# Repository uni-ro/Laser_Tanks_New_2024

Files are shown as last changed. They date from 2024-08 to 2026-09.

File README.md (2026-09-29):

# Laser Tanks
Laser Tanks is a project run by the Curtin Robotics Club.
Our aim is to make a game of laser tag that is played with remote controlled tanks.
hi from james

## Contents
- [Code](https://github.com/curtinrobotics/Laser_Tanks_New_2024/tree/master/Code)
- [Laser Reciever](https://github.com/curtinrobotics/Laser_Tanks_New_2024/tree/master/Laser%20Receiver)
- [Tank CAD Model](https://github.com/curtinrobotics/Laser_Tanks_New_2024/tree/master/Tank%20CAD%20Model)
- [Tank Motherboard](https://github.com/curtinrobotics/Laser_Tanks_New_2024/tree/master/Tank%20Motherboard)

***

### CAD model
This is the documentation for the tank CAD model.
![[CAD Model#Summary]]

***

### Motherboard
This is the documentation for the tank motherboard.

![[Tank Motherboard]]

***

### Microcontroller Programming  
![[How to write and upload code]]

***

### Remote microcontroller programming  

***

### Laser Detection  

***

### Map Design  

***

### RFID

***

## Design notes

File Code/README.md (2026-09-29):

# Code
This is the guide for how to write code and upload the code to the ESP8266 and ESP32s for Laser Tanks.

## Environment setup
1. **Download VSCode**.
	The programming IDE we are using is Visual Studio Code. You can download it from here: https://code.visualstudio.com/download

2. **Install the required extensions**.
	The required extensions are
	- PlatformIO
	- C/C++
	The recommended extensions are
	- Serial Monitor

3. **Open the the Tank Source folder in VSCode**.
	Once you have VSCode set up, you can open the Tank Source folder. This folder contains everything for programming and uploading. You will know you have opened the correct folder if your explorer looks like this.
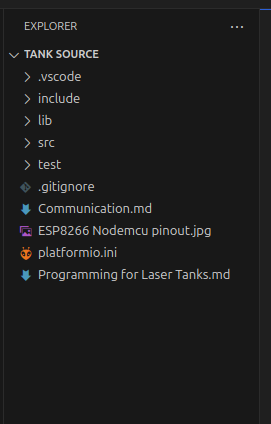
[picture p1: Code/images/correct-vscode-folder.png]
correct vscode folder
	 

## Minimal example
This is an example of how to get a code file compiled and uploaded to the microcontrollers.

### Create the code file
Under the src folder, create a new .cpp file to write the code in.
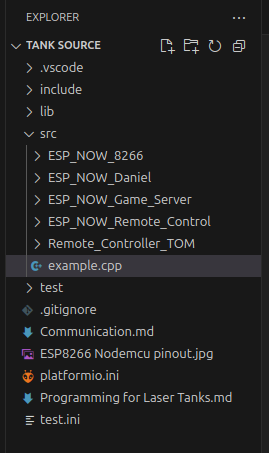
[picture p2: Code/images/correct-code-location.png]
correct code location

The code file needs a few things in it before it can be compiled and uploaded

```cpp title="Minimal example"
#include <Arduino.h>

void setup() {

}

void loop() {

}
```

### Create the platformio.ini configuration.
In order to actually upload to the microcontrollers, you need to create a platformio configuration.
An example platformio configuration looks like this
```ini title="Example platformio"
[env:Configuration_name]
platform = platform_name
board = board_name
framework = framework_name
build_src_filter =
	-<**/*.cpp>
```
- env is the name of your configuration. Put whatever you want there ```[env:Whatever]```
- platform_name refers to the microcontroller you are using. For example ```board = espressif32``` for the ESP32, and ```board = espressif8266``` for the ESP8266.
- board_name refers to what board you are using. If you are unsure, use ```board = nodemcu```
- framework refers to, i dont know just put ```framework = arduino```
- build_src_filter is where you tell platformio which files to compile. Make sure you include the line ```-<**/*.cpp>```. This tells platformio to ignore every code file in the src directory, without this, platformio will try to compile every file at the same time which will lead to errors. Include ```+<path_to_file.cpp>``` for every file you want to include in your configuration. For this example, this will be ```+<example.cpp>```

### Upload to the microcontroller
Now we are ready to upload the code to the microcontroller. First go to the platformio tab on the left.
![[Pasted image 20250313174216.png]]
Then, expand the option with the same name that you put in the ```[env:Whatever]``` and click Upload.
![[Pasted image 20250313174403.png]]

## Troubleshooting
### Board is not detected
If your computer is not detecting the microcontroller

### Uploading through wsl

First install usbipd to windows, if not already installed. To install usbipd, use the command ```winget install usbipd``` in the windows command line
Open a powershell window or command prompt in administrator mode.
Use the command ```usbipd list``` to find a list of all connected usb devices.
Find the device required and take note of the bus id under the "BUSID" column.
If this is the first time connecting the device, run the command ```usbipd bind -b {BUSID}``` where {BUSID} is the id of the usb to attach
Next, attach this to the wsl system by using the following command ```usbipd attach --wsl --busid {BUSID}``` where {BUSID} is still the id of the usb to attach.
This should attach the usb to the wsl system.
In wsl, run ```dmesg``` to find which port the device was attached to.
If the port is not found, run the following command ```sudo modprobe cp210x```. The port should now be found.
VSCode may state that there is an access denied error which can be fixed by running ```sudo chmod 777 {PORT}``` where {PORT} is the full path to the attached usb port.

This is also explained in the following guide: https://developer.espressif.com/blog/espressif-devkits-with-wsl2/

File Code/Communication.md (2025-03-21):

This is the communication between the tank and controller.
The tank communicates using both Serial and ESPNow.

The communication is very simple in an effort to make it more expandable.
The first byte, ignoring start byte for serial, is the message header and signifies what kind of message you are sending.
The rest of the message can be used however in accordance to the kind of message header.
The only restriction is bytes ```0xFF``` and ```0xFE```. These are reserved for the serial start and end bytes. Even when using ESPNow these bytes may not be used.
The maximum length of a message is 255 bytes, we should not even be getting close to this.

There is a difference between Serial and ESPNow. The difference is that ESPNow is sent and recieved as the entire message, no start of message or end of message bytes are needed. Serial however, is sent only 1 byte at a time. This means that a start byte and end byte is required.

## Serial communication differences
Serial communication requires an extra byte marking the start of the message, and an extra one for the end of message.
The start of the message is signified by a ```0xFF``` or ```255```
The end of the message is signified by a ```0xFE``` or ```254```

## ESPNow communication differences
ESPNow handles the protocol for you, as such a start byte and end byte is not included.

## Messages
Here is a list of all the message types and how to use them

| First byte | Message type |
| --- | --- |
| 0x00 | Ping |
| 0x01 | Left motor speed  |
| 0x02 | Right motor speed |

### Ping - 0x00
The ping message is used to check if the controller is communicating with the tank, or if the tank is communicating with the controller. 

|Byte number|Options|Description|
|---|---|---|
|0|0x00|Signifies the message type is a ping|
|1|0x00 or 0x01|Signifies whether the message is a ping - 0x00, or a response to a ping 0x01|

### Left motor speed - 0x01
This message is used to tell the tank to set the left motor to a specific speed

| Byte number | Options | Description |
| --- | --- | --- |
| 0 | 0x01 | Signifies the message type is setting the left motor speed |
| 1 | 0x00 - 0x3F, 0x40 - 0x7F | Speed and direction of the motor. Forward between 0x00 - 0x3F where 0x00 is slowest and 0x3F is fastest. Backward between 0x40 - 0x7F where 0x40 is slowest and 0x7F is fastest |

### Right motor speed - 0x02
This message is used to tell the tank to set the right motor to a specific speed

| Byte number | Options | Description |
| --- | --- | --- |
| 0 | 0x02 | Signifies the message type is setting the right motor speed |
| 1 | 0x00 - 0x3F, 0x40 - 0x7F | Speed and direction of the motor. Forward between 0x00 - 0x3F where 0x00 is slowest and 0x3F is fastest. Backward between 0x40 - 0x7F where 0x40 is slowest and 0x7F is fastest |

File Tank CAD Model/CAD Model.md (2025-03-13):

## Summary
This is where all the different versions of the tank 3D model are stored.
Each different version was 3D printed, tested and then improved upon.
This is the current version
![[Tank model V4#Overview]]

## Versions

- [[Tank model V2]]
- [[Tank model V3]]
- [[Tank model V4]]

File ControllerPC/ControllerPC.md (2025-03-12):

This is the code that will run on your computer and control the laser tank.

TODO: Write more here

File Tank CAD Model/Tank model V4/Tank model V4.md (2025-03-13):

## Overview
This is the 4th version of the Laser Tank model. It aims to address issues in the V3 model such as
- The screw holes being slightly too small
- The axle holes being slightly too small
- The driver wheel being too close to the idler wheel
- The accidental shallow screw inset holes in the front track holder
- The holder for the switch and two LEDs being too thin
- The corner of the front track holders needing to be clipped to fit properly

A big change made in V4 is the back tracks not being adjustable anymore. Instead, the tracks were modelled and measured. The required length of tracks was found to be roughy 356 mm
![[Pasted image 20250123214053.png|1400]]

![[IMG_2936.jpg|1400]]
![[IMG_2934.jpg|700]] ![[IMG_2935.jpg|700]]

## Parts
These are the parts needed to build the Tank model V4. It reflects roughly the total cost of building this from scratch.

|Part|Supplier|Cost|
|---|---|---|
|ESP826 Dev board|https://www.makerstore.com.au/product/elec-nodemcu-esp8266/|$14|
|Twin motor gearbox|https://www.pololu.com/product/61|$21|
|Track and wheel set|https://core-electronics.com.au/tamiya-70100-track-and-wheel-set.html|$23|
|2S Li-Po battery|https://hobbytechtoys.com.au/products/hpi-plazma-7-4v-600mah-10c-lipo-battery-pack-160838|$20|
|Total| |$78|

This table does not include everything. For example the breadboard, and wires and stuff.

## Advantages
- Having the back tracks be at a fixed position improves the visuals of the back of the tank. We no longer have an awkward overhanging area
![[back of tank.jpg|700]]

- Having the back tracks be at a fixed position removes the long thin section of PLA that is prone to bending
![[bendy back.jpg|700]] ![[non bendy back.jpg|700]]

- The section that holds the switch and LEDs holds them really firmly and nicely. Giving enough room to connect wires to it
![[switch holder.jpg|700]]

- The section that holds the protoboard holds it really nicely and firmly while being not too difficult to slide in
![[proto board 1.jpg|700]] ![[proto board 2.jpg|700]]

## Issues

- One of the clips that hold the protoboard is broken 
- ![[broken clip.jpg|800]]

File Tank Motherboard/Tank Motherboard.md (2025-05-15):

Here is the documentation for the tank motherboard.

Versions
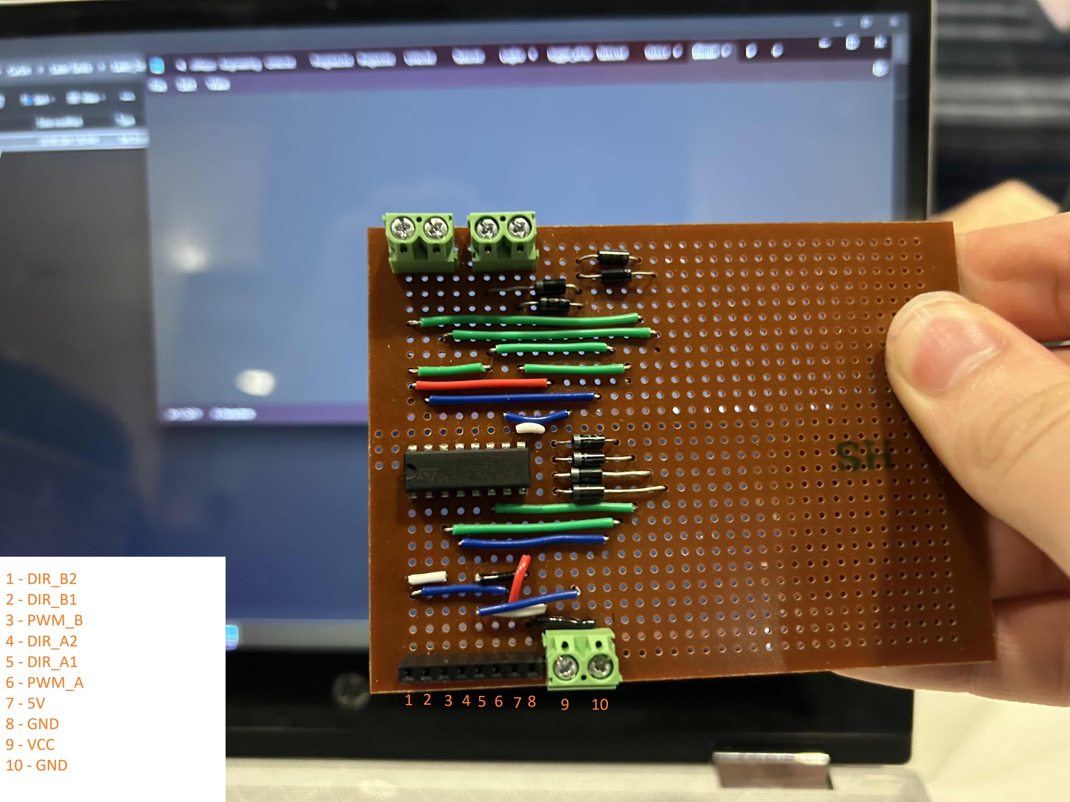
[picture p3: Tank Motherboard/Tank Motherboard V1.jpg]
- 
- [[Tank Motherboard V2.excalidraw]]
- [[Tank Motherboard V3]]

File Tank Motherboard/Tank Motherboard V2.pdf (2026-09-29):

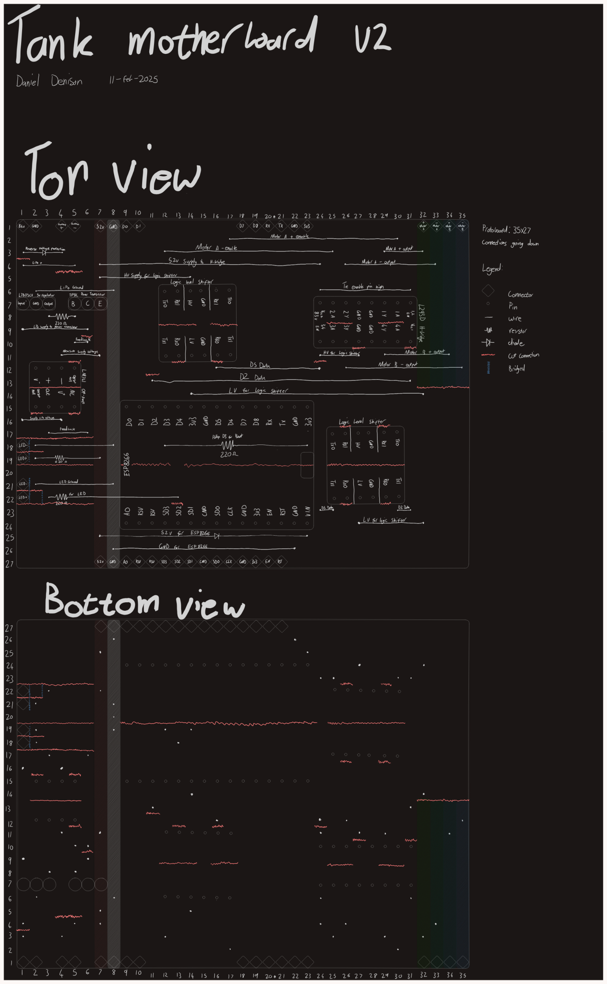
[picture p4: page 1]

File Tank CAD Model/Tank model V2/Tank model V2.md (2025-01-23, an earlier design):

## Overview
This is the 2nd version of the Laser Tanks model.

![[IMG_2780.jpg|1000]]
![[IMG_2781.jpg|500]] ![[IMG_2782.jpg|500]]

## Parts
These are the parts needed to build the Tank model V2. It reflects roughly the total cost of building this from scratch.

|Part|Supplier|Cost|
|---|---|---|
|ESP826 Dev board|https://www.makerstore.com.au/product/elec-nodemcu-esp8266/|$14|
|Twin motor gearbox|https://www.pololu.com/product/61|$21|
|Track and wheel set|https://core-electronics.com.au/tamiya-70100-track-and-wheel-set.html|$23|
|2S Li-Po battery|https://hobbytechtoys.com.au/products/hpi-plazma-7-4v-600mah-10c-lipo-battery-pack-160838|$20|
|Total| |$78|

This table does not include everything. For example the breadboard, and wires and stuff.

## Advantages
- Using nuts where they are being pulled further into their sockets works very well
![[Nuts being pulled in are good.jpg|500]]

## Issues

- Because the tank tracks are under tension, they are pulling the front track holders and the back track holders together, causing the top plate to bend
![[Top plate bending.jpg|500]]

- The breadboard holder is a little bit too short
![[Badly sized breadboard holder.jpg|500]]

- The motor driver circuit is places as far as possible from the motors. For some reason...

- The tank tracks have a large footprint on the ground which adds a bunch of friction while turning

- The channels the screws holding the back track holders screw into are too thin. They are being bent outwards by the screws
![[Not enough screw clearance.jpg|500]]

- The tank is a little bit too wide. The wheels are popping off

- Nuts appear to be unsuitable for screwing screws into, where the nuts are being pulled out.
![[Nuts being pulled out are bad.jpg|500]]
Superglue was even used here to secure the nuts in place but it doesnt seem to be enough.

- No propper place to put a battery, battery is secured with cable ties

- No propper place to put the motor driver, the circuit is secured in with cable ties

- There is nowhere for a switch to go

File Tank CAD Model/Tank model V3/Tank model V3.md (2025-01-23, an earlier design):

## Overview
This is the 3rd version of the Laser Tank model.
This version addresses some of the problems realised with V2, namely
- The motor driver circuit being far from the motors
- The channels for the screws for the back tracks being too small
- Nowhere for a switch to go

Version 3 also includes a space for 2 LEDs for showing anything

![[V3 pic 1.jpg|1200]]
![[V3 pic 2.jpg|600]] ![[V3 pic 3.jpg|600]]

## Parts
These are the parts needed to build the Tank model V3. It reflects roughly the total cost of building this from scratch.

|Part|Supplier|Cost|
|---|---|---|
|ESP826 Dev board|https://www.makerstore.com.au/product/elec-nodemcu-esp8266/|$14|
|Twin motor gearbox|https://www.pololu.com/product/61|$21|
|Track and wheel set|https://core-electronics.com.au/tamiya-70100-track-and-wheel-set.html|$23|
|2S Li-Po battery|https://hobbytechtoys.com.au/products/hpi-plazma-7-4v-600mah-10c-lipo-battery-pack-160838|$20|
|Total| |$78|

This table does not include everything. For example the breadboard, and wires and stuff.

## Advantages
- The threaded inserts work very well. If you make the part fit the smaller diameter at the front of the insert and fit the entire length. They are very easy to insert with a soldering iron and will grip on much tighter than a hex nut
![[Threaded insert.jpg|500]]
- The screw inset depth is perfect to make these rounded M3 screws flush with the top of the body
![[Flush screws.jpg|500]]

## Issues
- Holes for the axles to go through are still too small, needing to hammer the axles in
![[Small axles.jpg|500]]
- Holes for the threaded inserts in the front tracks were accidentally too shallow. 
- The driver wheel is too close to the idler wheel next to it. When using tight tracks, they rub against each other causing a lot of friction
![[Driver and idler wheel too close.jpg|500]]
- The section for fitting the switch and LEDs is too thin. It broke apart while I was trying to remove the support structure
![[Switch and LED holder too thin.jpg|500]]
- The front track holders get too close to the screw holes for the gearbox. The corners need to be cut so that it can fit
![[Cut corners.jpg|500]]
- The holes for the screws are a tiny bit too small, the screws don't fall easily through the holes. Not really an issue because the screws can be easily screwed through, but would be nicer if that was not needed

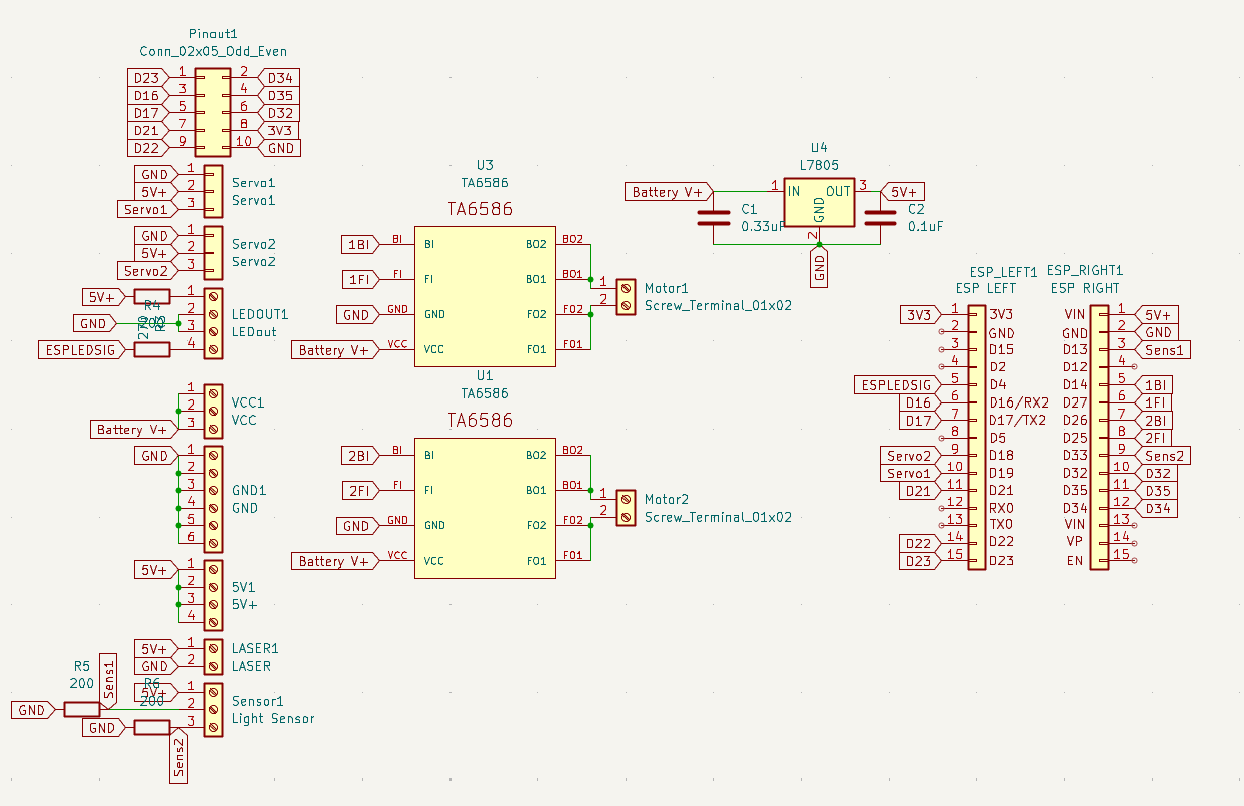
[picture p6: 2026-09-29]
Tank Motherboard/LasertanksPCB_KiCad/motorcontroller/LaserTankPCBV1_Schematic.png

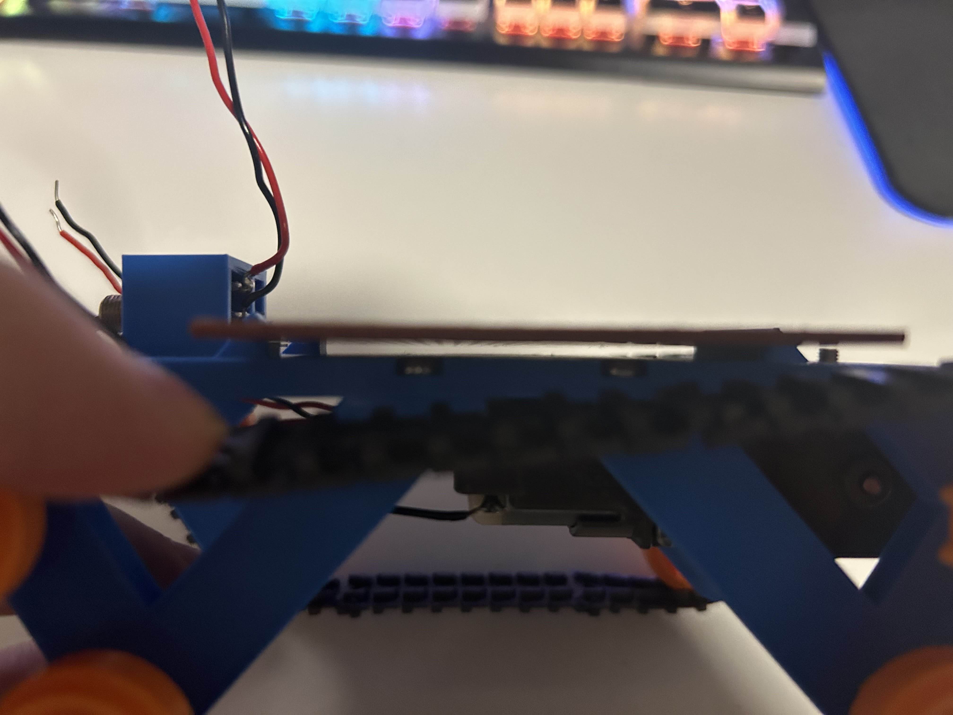
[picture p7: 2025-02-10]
Tank CAD Model/Tank model V4/proto board 2.jpg

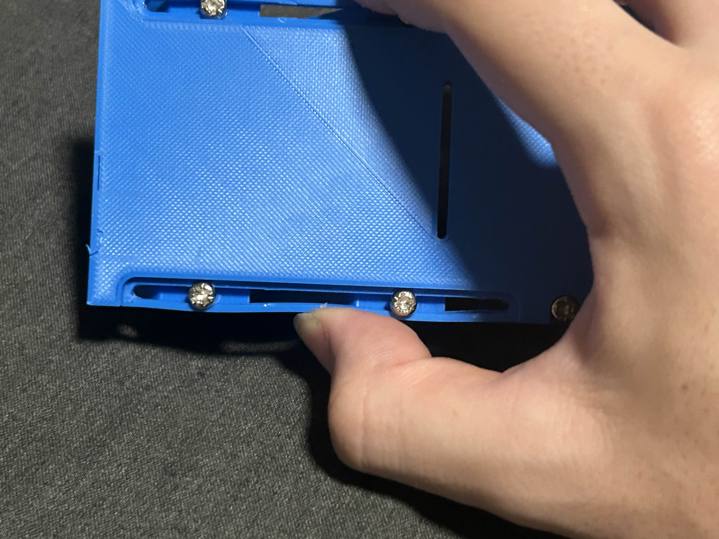
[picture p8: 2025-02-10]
Tank CAD Model/Tank model V4/bendy back.jpg

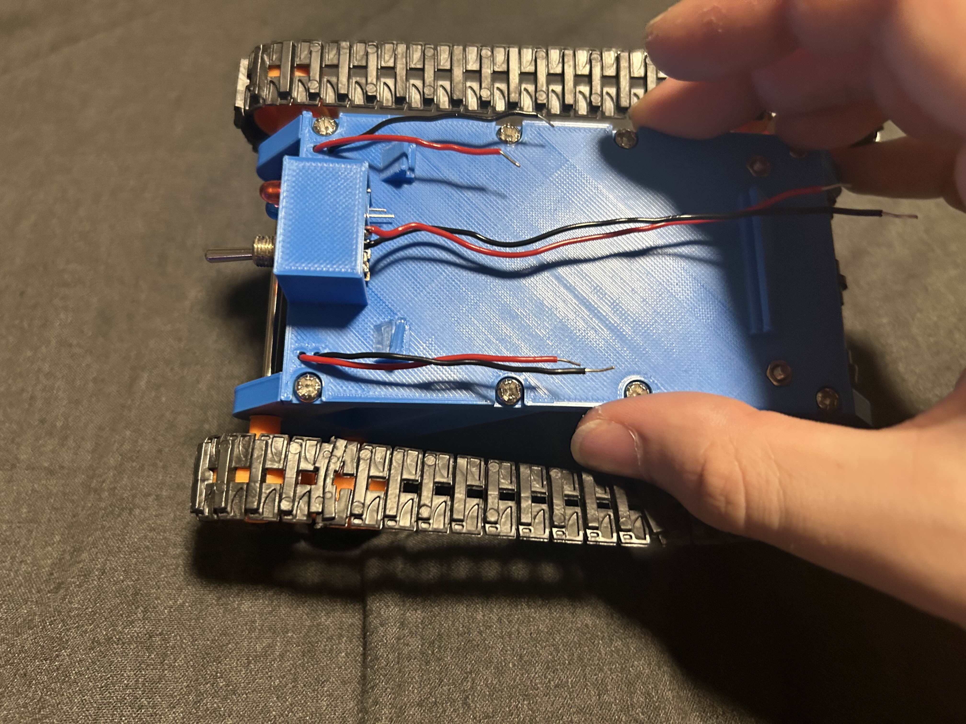
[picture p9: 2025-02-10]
Tank CAD Model/Tank model V4/non bendy back.jpg

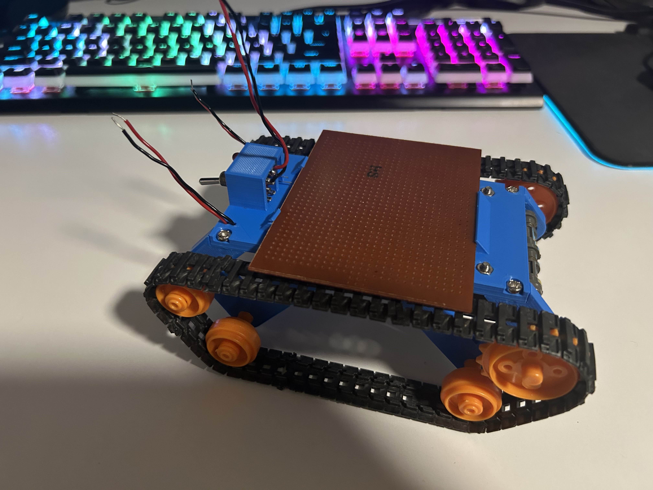
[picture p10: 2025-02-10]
Tank CAD Model/Tank model V4/proto board 1.jpg

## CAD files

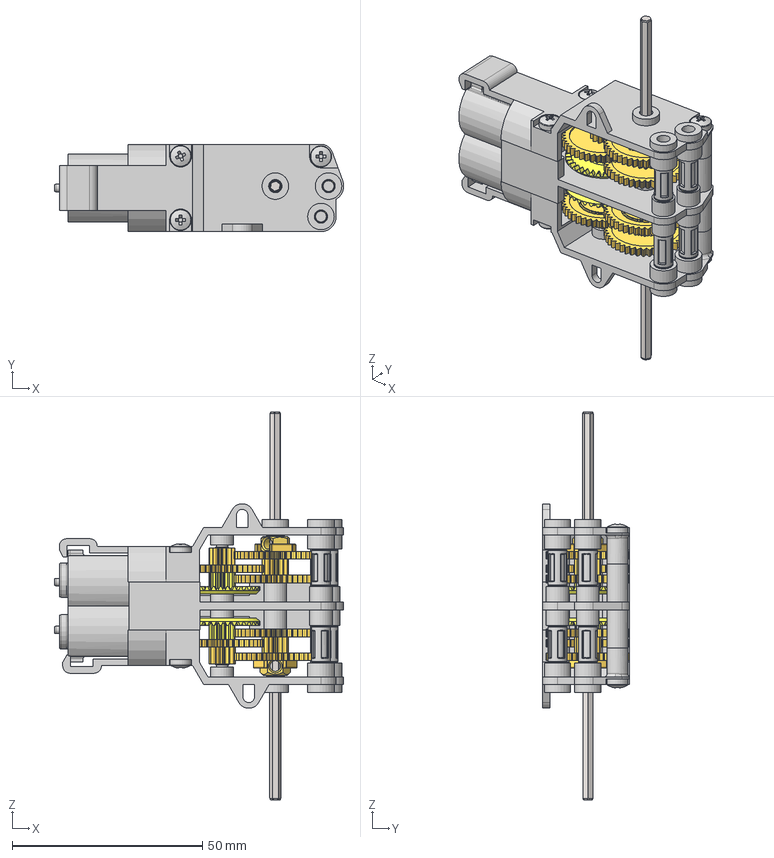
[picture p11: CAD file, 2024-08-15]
Tank CAD Model/STEP files/Motor.step
76.1 x 23.0 x 102.0 mm
middle
motor_1 x 2
left
right
DG_brass_gap4.0 x 12
DG_gold_brass x 2
DG_purple_8_mtr x 2
DG_shaft_23mm x 2
DG_shaft_50mm x 2
DG_yellow_34_12_N01 x 2
TG_G3 x 2
TG_G2 x 4
middle pin x 4
Pan Head Cross Recess Screw_DIN x 6

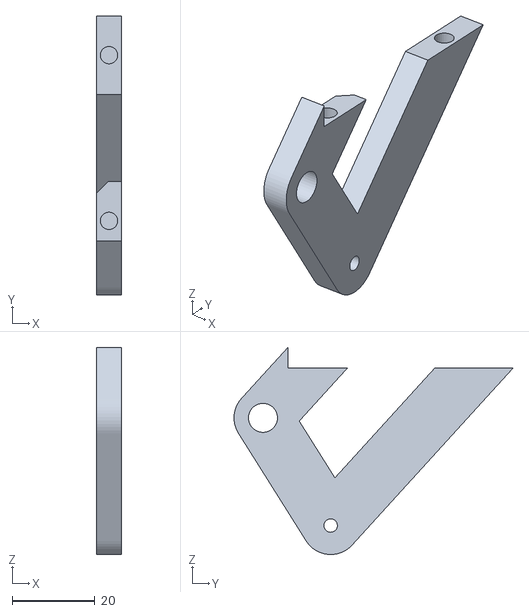
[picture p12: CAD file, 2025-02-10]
Tank CAD Model/Tank model V4/Front track holder L.stl
6.00 x 67.4 x 50.0

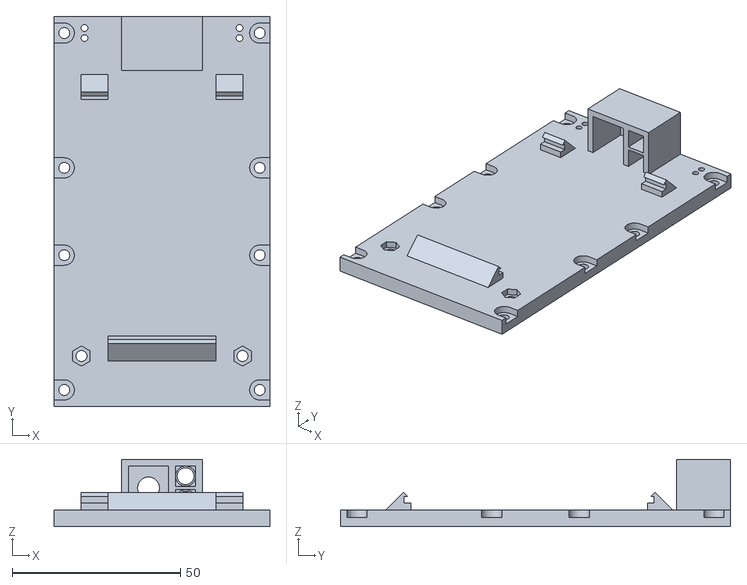
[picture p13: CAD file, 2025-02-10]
Tank CAD Model/Tank model V4/Top plate.stl
64.0 x 115.8 x 20.0

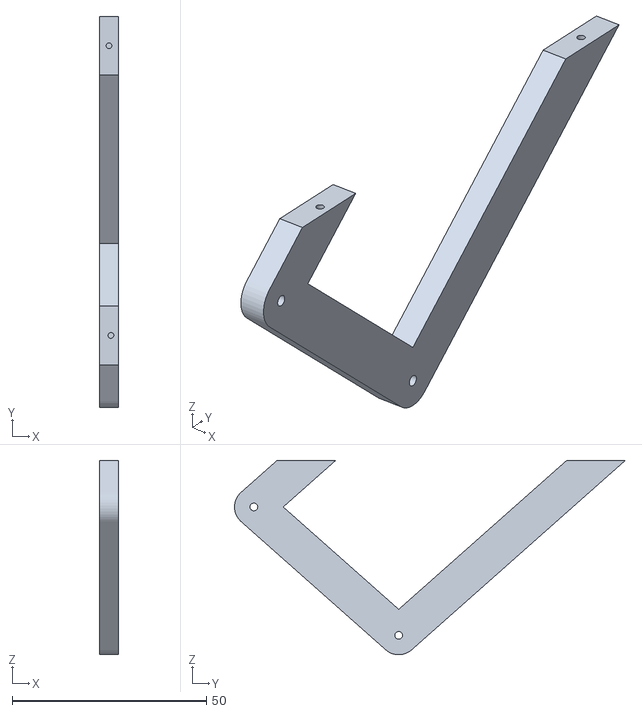
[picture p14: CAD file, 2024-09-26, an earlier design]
Tank CAD Model/Tank model V1/Front track.stl
5.00 x 100.5 x 50.0

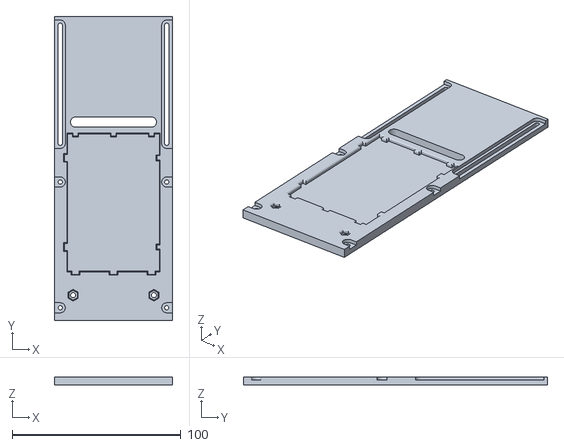
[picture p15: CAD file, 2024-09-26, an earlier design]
Tank CAD Model/Tank model V2/Top plate.stl
70.0 x 180.0 x 5.00

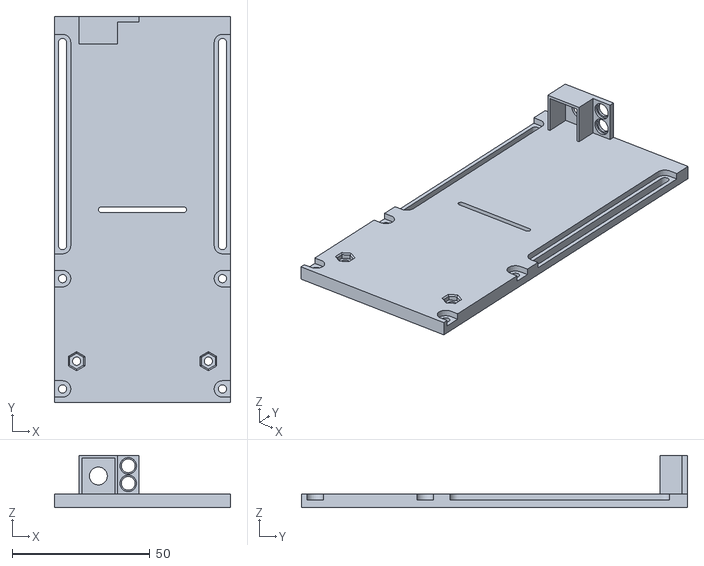
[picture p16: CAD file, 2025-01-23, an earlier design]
Tank CAD Model/Tank model V3/Top plate.stl
64.0 x 140.0 x 19.0

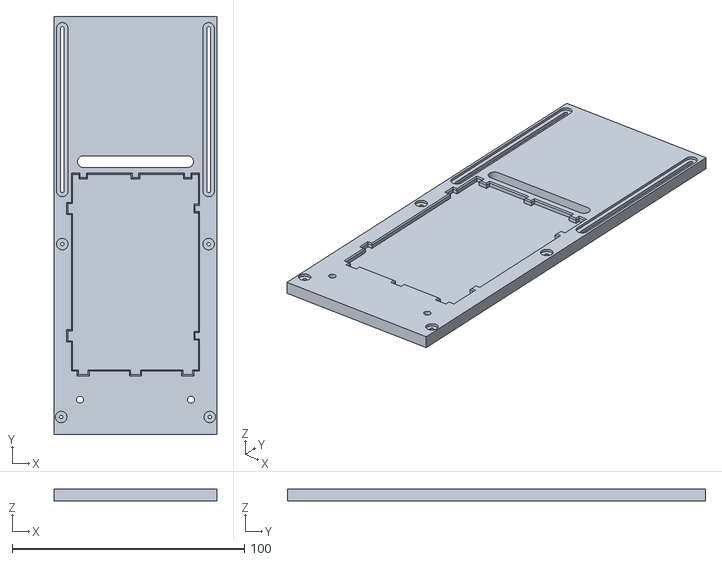
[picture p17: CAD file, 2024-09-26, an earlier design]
Tank CAD Model/Tank model V1/Top plate.stl
70.0 x 180.0 x 5.00

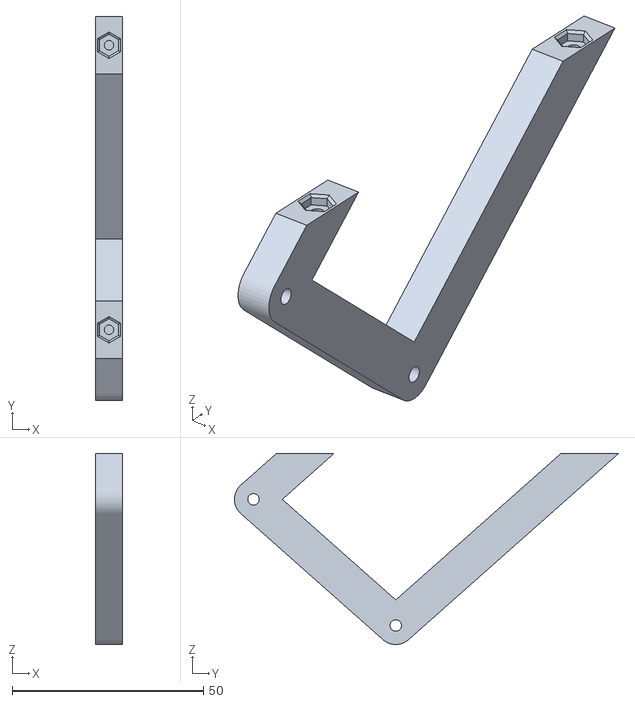
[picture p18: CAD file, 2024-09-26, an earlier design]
Tank CAD Model/Tank model V2/Front track holder.stl
7.00 x 100.5 x 50.0

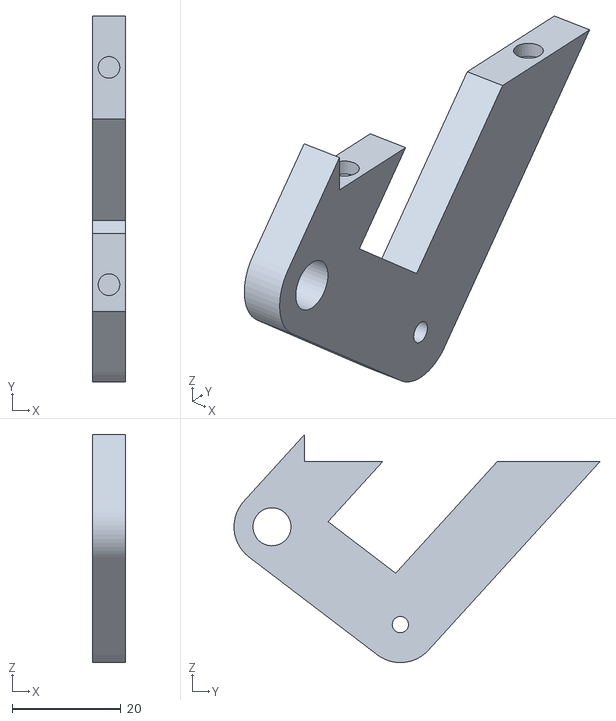
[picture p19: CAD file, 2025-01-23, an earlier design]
Tank CAD Model/Tank model V3/Front track holder.stl
6.00 x 67.4 x 42.0

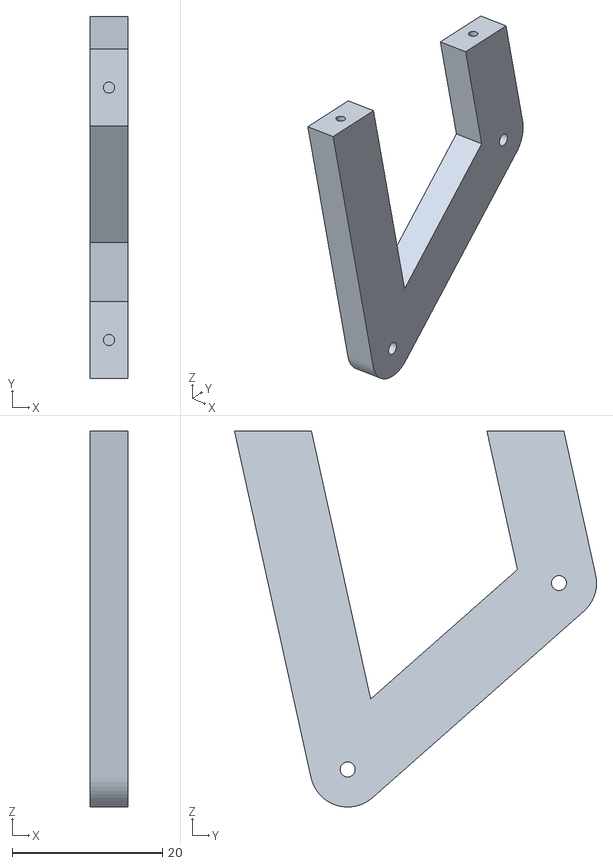
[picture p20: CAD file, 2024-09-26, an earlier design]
Tank CAD Model/Tank model V1/Back track.stl
5.00 x 48.1 x 50.0

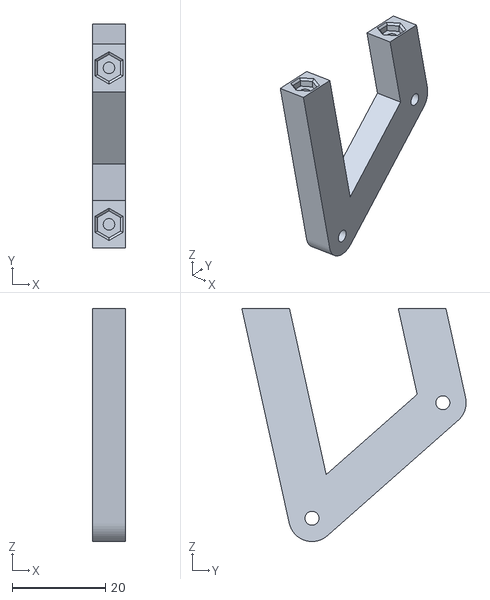
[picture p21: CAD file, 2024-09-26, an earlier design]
Tank CAD Model/Tank model V2/Back track holder.stl
7.00 x 48.1 x 50.0

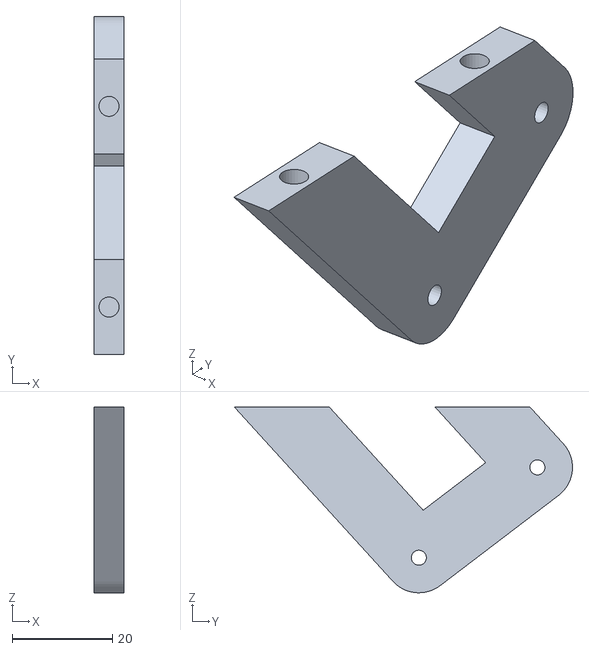
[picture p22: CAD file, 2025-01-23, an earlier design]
Tank CAD Model/Tank model V3/Back track holder.stl
6.00 x 67.4 x 37.0

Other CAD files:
Tank CAD Model/Tank model V4/Back track holder.stl
Tank CAD Model/Tank model V4/Front track holder R.stl
Tank CAD Model/Tank model V1/Top plate skew.stl

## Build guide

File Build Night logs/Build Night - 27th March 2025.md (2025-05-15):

- Tom is helping Blake learn to program on an arduino nano. Trying to blink a laser diode
- Got Thomas started on the turret for the tank. Invited him to the Fusion360 group.
- Emma and Gabriel are mucking around with the raspberry pi.

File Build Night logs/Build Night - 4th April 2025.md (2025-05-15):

- Blake and Tom working on ramping up motor
- Emma is workign on stopping the tank if the controller disconnects

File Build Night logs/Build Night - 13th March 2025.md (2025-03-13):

## Attendees
- Daniel
- Tom
- Gabriel
- Blake
- Silas
- Emma

## Progress
- We have been struggling with an issue with the motors on the tank. We are using little DC motors with gears attached to drive the tracks. However, the gear that attaches to one of the motors was not propperly joined to the motor, causing the motor shaft to spin without turning the tracks. We found 2 motors in the club room that have the gears propperly attaches. We swapped out the bad motor for the good one and the tank is now driving like perfect again.
- I (Daniel) have been designing a PCB to replace the protoboard on the current tank. A PCB is going to be way smaller and cleaner than anything I could do on the protoboard. The design is not finished yet, but I will order it ASAP.
- Once the PCB arrives Ill (Daniel) start working on the next version of the tank model. I will design it to propperly hold the PCB in place, probably with screws. 
- Gabriel came up with a concept for a turret
- We are getting really close to the point where we could attach and use a turret. Once wee have the PCB,

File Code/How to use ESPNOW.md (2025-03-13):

ESPNOW is the communication protocol we are using for the controller / tank communication.
ESPNOWs implementation differs depending on whether you are programming an ESP32 or ESP8266.

## ESPNOW for ESP32
This is how you implement ESPNOW for the ESP32.
### Header files
To use ESPNOW on the ESP32 you need to include the following header files
```cpp title="Required header files for ESPNOW on the ESP32"
#include <WiFi.h>
#include <esp_wifi.h>
#include <esp_now.h>
```

### Initialisation
To set up ESPNOW, use the following code in your setup function
```cpp title="ESPNOW setup code"
// Make sure the ESP32 is in the correct WiFi mode
WiFi.disconnect();
WiFi.mode(WIFI_STA);

uint8 peer_address[] = {0x00, 0x00, 0x00, 0x00, 0x00, 0x00}

esp_now_peer_info_t info;
info.channel = 0;
info.encrypt = false;
memcpy(info.peer_addr, slave_address, 6);

esp_now_init();
esp_now_add_peer(&info);
```

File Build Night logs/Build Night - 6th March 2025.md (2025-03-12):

## People
- Daniel
- Tom
- Gabriel
- Blake
- Silas
- Emma

## Progress
- Team building
- Gabriel working on battery holder
- Blake learning fusion, happy to work on the turret design
- Silas is working on laser reciever stuff
- Tom is working on the controller code
- Emma is working on controller code
- Steve is doing RFID

## Needed materials

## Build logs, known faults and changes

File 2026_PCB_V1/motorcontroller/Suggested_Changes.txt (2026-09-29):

Needs pin header for battery not terminal blocks
the traces between the battery to motor drivers to motor terminals seem a bit thin
should have a pin out headers for a motor rather than a servo and possibly another motor driver on the pcb as the turret has 1 dc motor plus servo not 2 servos
there are slight clearance issues at the top of the pcb due to the over hang from the esp32, though this is very minor 
might be helpful to have more pin headers rather than terminal blocks for breaking out the battery + and 5v  
Needs silkscreen labs for + and - on things like the led terminal blocks

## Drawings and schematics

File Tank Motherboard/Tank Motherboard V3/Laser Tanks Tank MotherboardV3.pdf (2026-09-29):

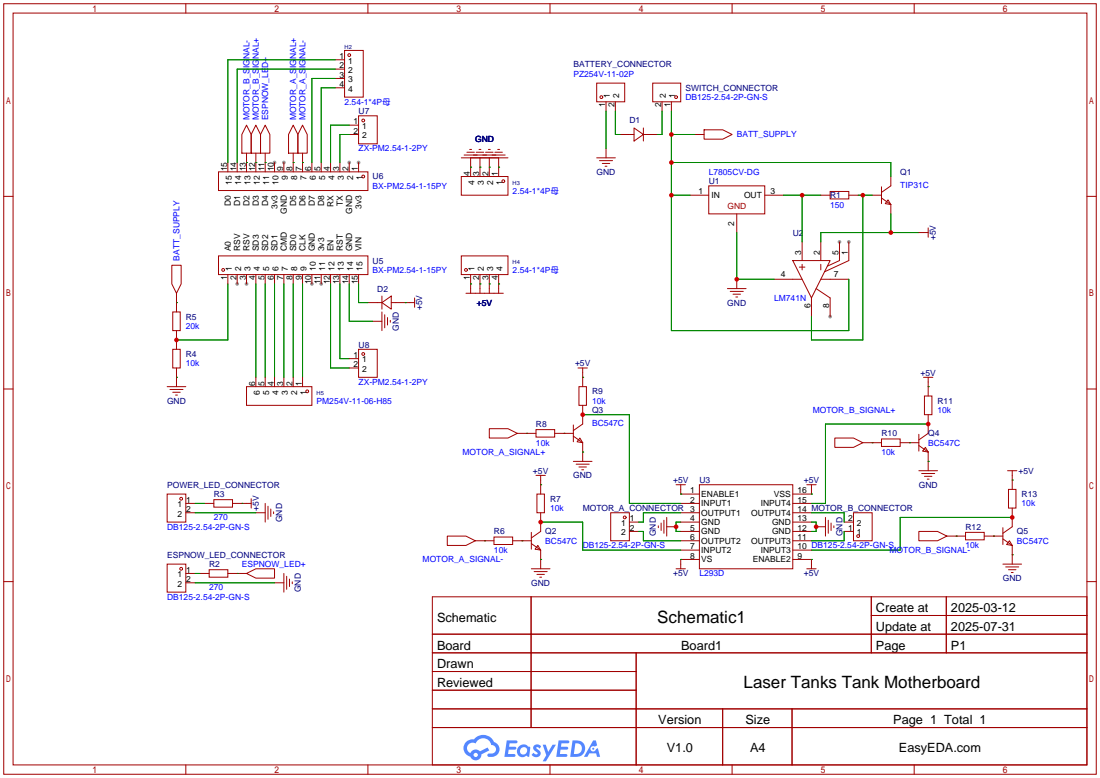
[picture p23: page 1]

Schematic | Schematic1 | Create at | 2025-03-12

Update at | 2025-07-31

Board | Board1 | Page | P1
Drawn | | Laser Tanks Tank Motherboard
Reviewed

Version | Size | Page 1 Total 1
V1.0 | A4 | EasyEDA.com

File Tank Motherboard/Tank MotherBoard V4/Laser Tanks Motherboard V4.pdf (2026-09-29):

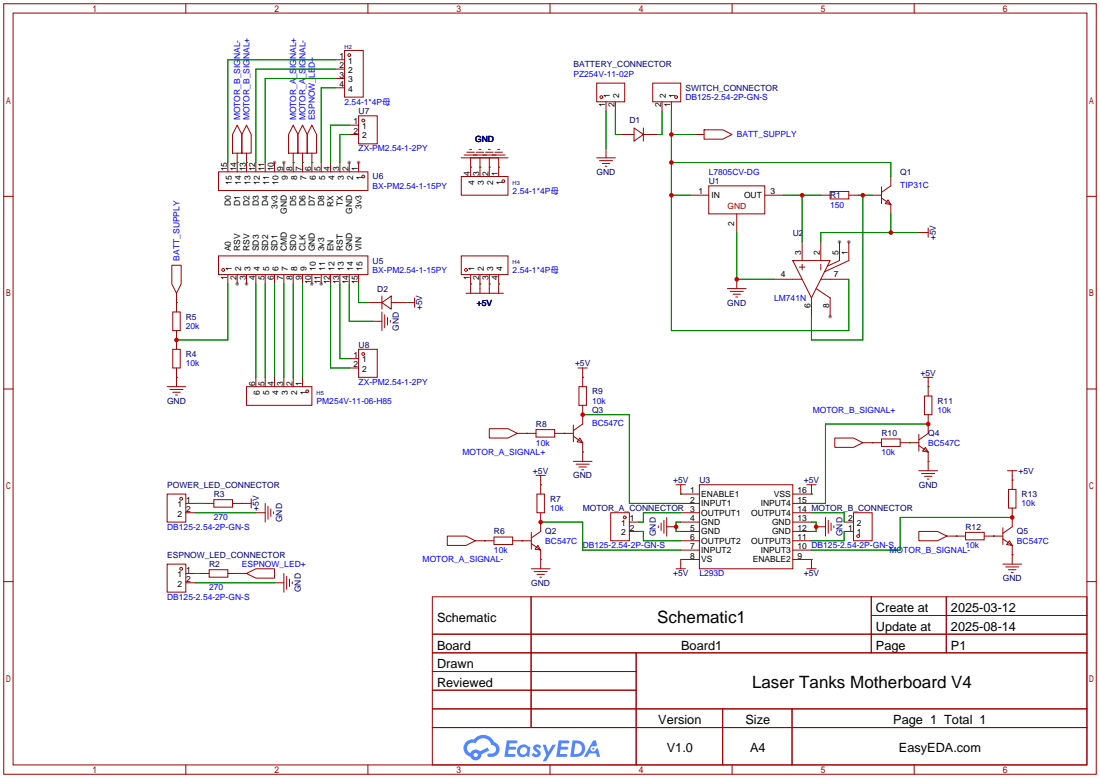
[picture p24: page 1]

Schematic | Schematic1 | Create at | 2025-03-12

Update at | 2025-08-14

Board | Board1 | Page | P1
Drawn | | Laser Tanks Motherboard V4
Reviewed

Version | Size | Page 1 Total 1
V1.0 | A4 | EasyEDA.com

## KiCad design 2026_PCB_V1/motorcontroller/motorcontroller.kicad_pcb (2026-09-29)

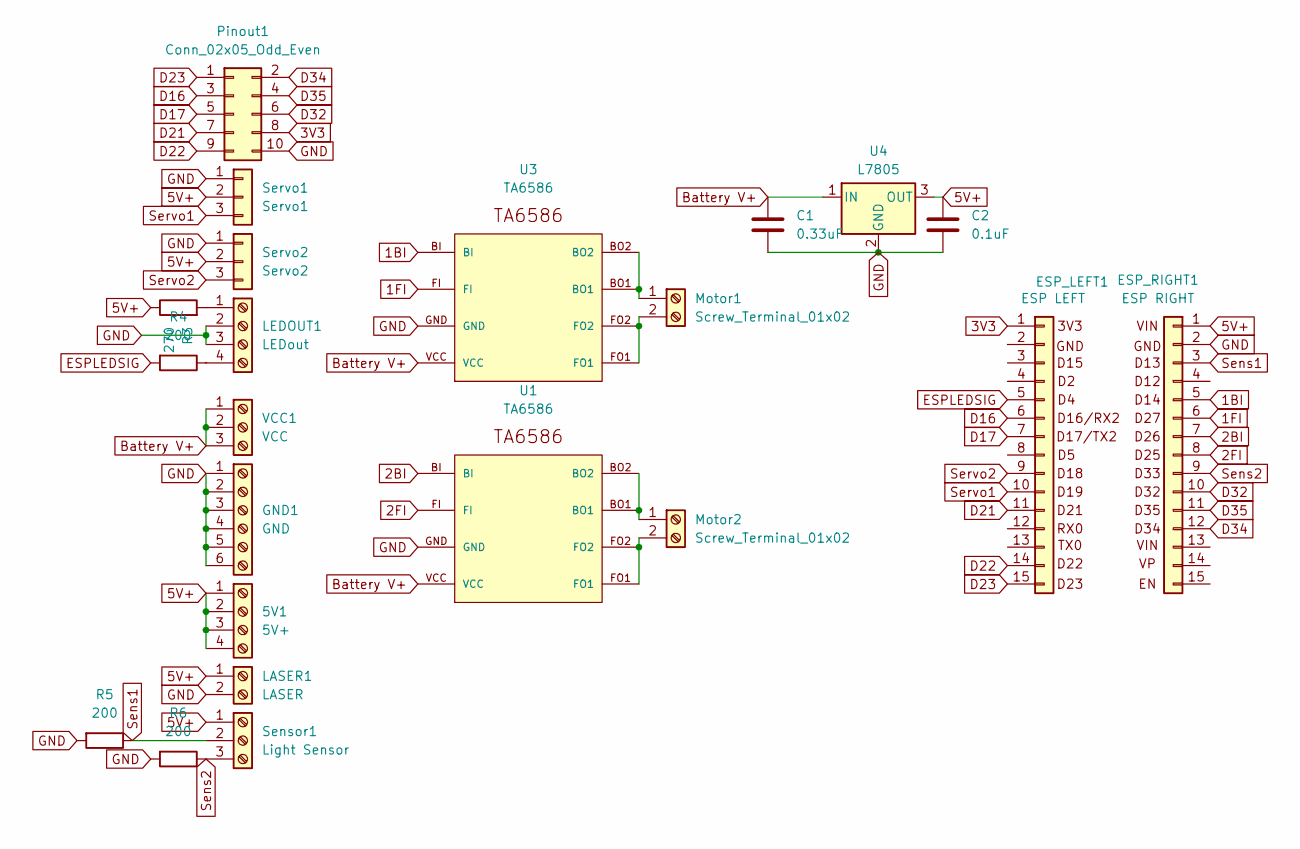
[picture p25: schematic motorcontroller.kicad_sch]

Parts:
5V1: 5V+; TerminalBlock_4Ucon_1x04_P3.50mm_Horizontal
C1: 0.33uF; C_Rect_L9.0mm_W2.5mm_P7.50mm_MKT
C2: 0.1uF; C_Rect_L9.0mm_W2.5mm_P7.50mm_MKT
ESP_LEFT1: ESP LEFT; PinHeader_1x15_P2.54mm_Vertical
ESP_RIGHT1: ESP RIGHT; PinHeader_1x15_P2.54mm_Vertical
GND1: GND; TerminalBlock_4Ucon_1x06_P3.50mm_Horizontal
LASER1: LASER; TerminalBlock_4Ucon_1x02_P3.50mm_Horizontal
LEDOUT1: LEDout; TerminalBlock_4Ucon_1x04_P3.50mm_Horizontal
Motor1, Motor2: Screw_Terminal_01x02; TerminalBlock_4Ucon_1x02_P3.50mm_Horizontal
Pinout1: Conn_02x05_Odd_Even; PinHeader_2x05_P2.54mm_Vertical
R3: 270; R_Axial_DIN0207_L6.3mm_D2.5mm_P10.16mm_Horizontal
R4, R5, R6: 200; R_Axial_DIN0207_L6.3mm_D2.5mm_P10.16mm_Horizontal
Sensor1: Light Sensor; TerminalBlock_4Ucon_1x03_P3.50mm_Horizontal
Servo1: Servo1; PinHeader_1x03_P2.54mm_Vertical
Servo2: Servo2; PinHeader_1x03_P2.54mm_Vertical
U1, U3: TA6586; TA6586-FOOTPRINT
U4: L7805; TO-220F-3_Vertical
VCC1: VCC; TerminalBlock_4Ucon_1x03_P3.50mm_Horizontal

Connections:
1BI: ESP_RIGHT1.5 (D14), U3.BI
1FI: ESP_RIGHT1.6 (D27), U3.FI
2BI: ESP_RIGHT1.7 (D26), U1.BI
2FI: ESP_RIGHT1.8 (D25), U1.FI
3V3: ESP_LEFT1.1 (3V3), Pinout1.8
5V+: 5V1.1, 5V1.2, 5V1.3, 5V1.4, C2.1, ESP_RIGHT1.1 (VIN), LASER1.1, R3.1, Sensor1.1, Servo1.2, Servo2.2, U4.3 (OUT)
Battery V+: C1.1, U1.VCC, U3.VCC, U4.1 (IN), VCC1.1, VCC1.2, VCC1.3
D16: ESP_LEFT1.6 (D16), Pinout1.3
D17: ESP_LEFT1.7 (D17), Pinout1.5
D21: ESP_LEFT1.11 (D21), Pinout1.7
D22: ESP_LEFT1.14 (D22), Pinout1.9
D23: ESP_LEFT1.15 (D23), Pinout1.1
D32: ESP_RIGHT1.10 (D32), Pinout1.6
D34: ESP_RIGHT1.12 (D34), Pinout1.2
D35: ESP_RIGHT1.11 (D35), Pinout1.4
ESPLEDSIG: ESP_LEFT1.5 (D4), R4.2
GND: C1.2, C2.2, ESP_RIGHT1.2 (GND), GND1.1, GND1.2, GND1.3, GND1.4, GND1.5, GND1.6, LASER1.2, LEDOUT1.2, LEDOUT1.3, Pinout1.10, R5.2, R6.2, Servo1.1, Servo2.1, U1.GND, U3.GND, U4.2 (GND)
unnamed: LEDOUT1.1, R3.2
unnamed: LEDOUT1.4, R4.1
unnamed: Motor1.1, U3.BO1, U3.BO2
unnamed: Motor1.2, U3.FO1, U3.FO2
unnamed: Motor2.1, U1.BO1, U1.BO2
unnamed: Motor2.2, U1.FO1, U1.FO2
Sens1: ESP_RIGHT1.3 (D13), R5.1, Sensor1.2
Sens2: ESP_RIGHT1.9 (D33), R6.1, Sensor1.3
Servo1: ESP_LEFT1.10 (D19), Servo1.3
Servo2: ESP_LEFT1.9 (D18), Servo2.3

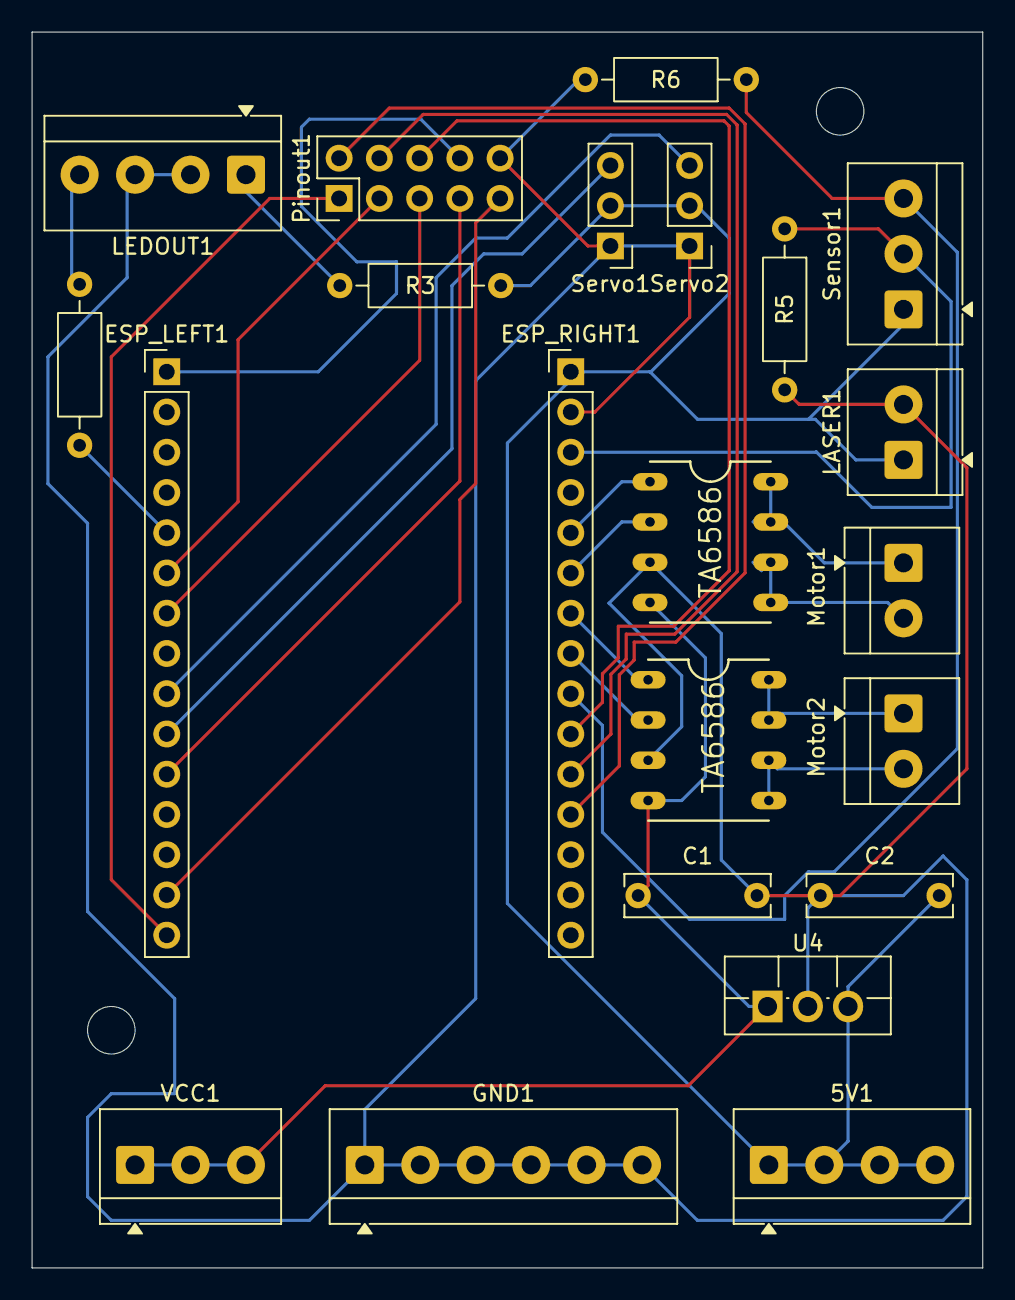
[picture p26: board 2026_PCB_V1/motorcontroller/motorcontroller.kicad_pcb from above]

Board: 2 copper layers, 60.0 x 78.0 mm, 22 parts (0 on the bottom side), 27 nets.

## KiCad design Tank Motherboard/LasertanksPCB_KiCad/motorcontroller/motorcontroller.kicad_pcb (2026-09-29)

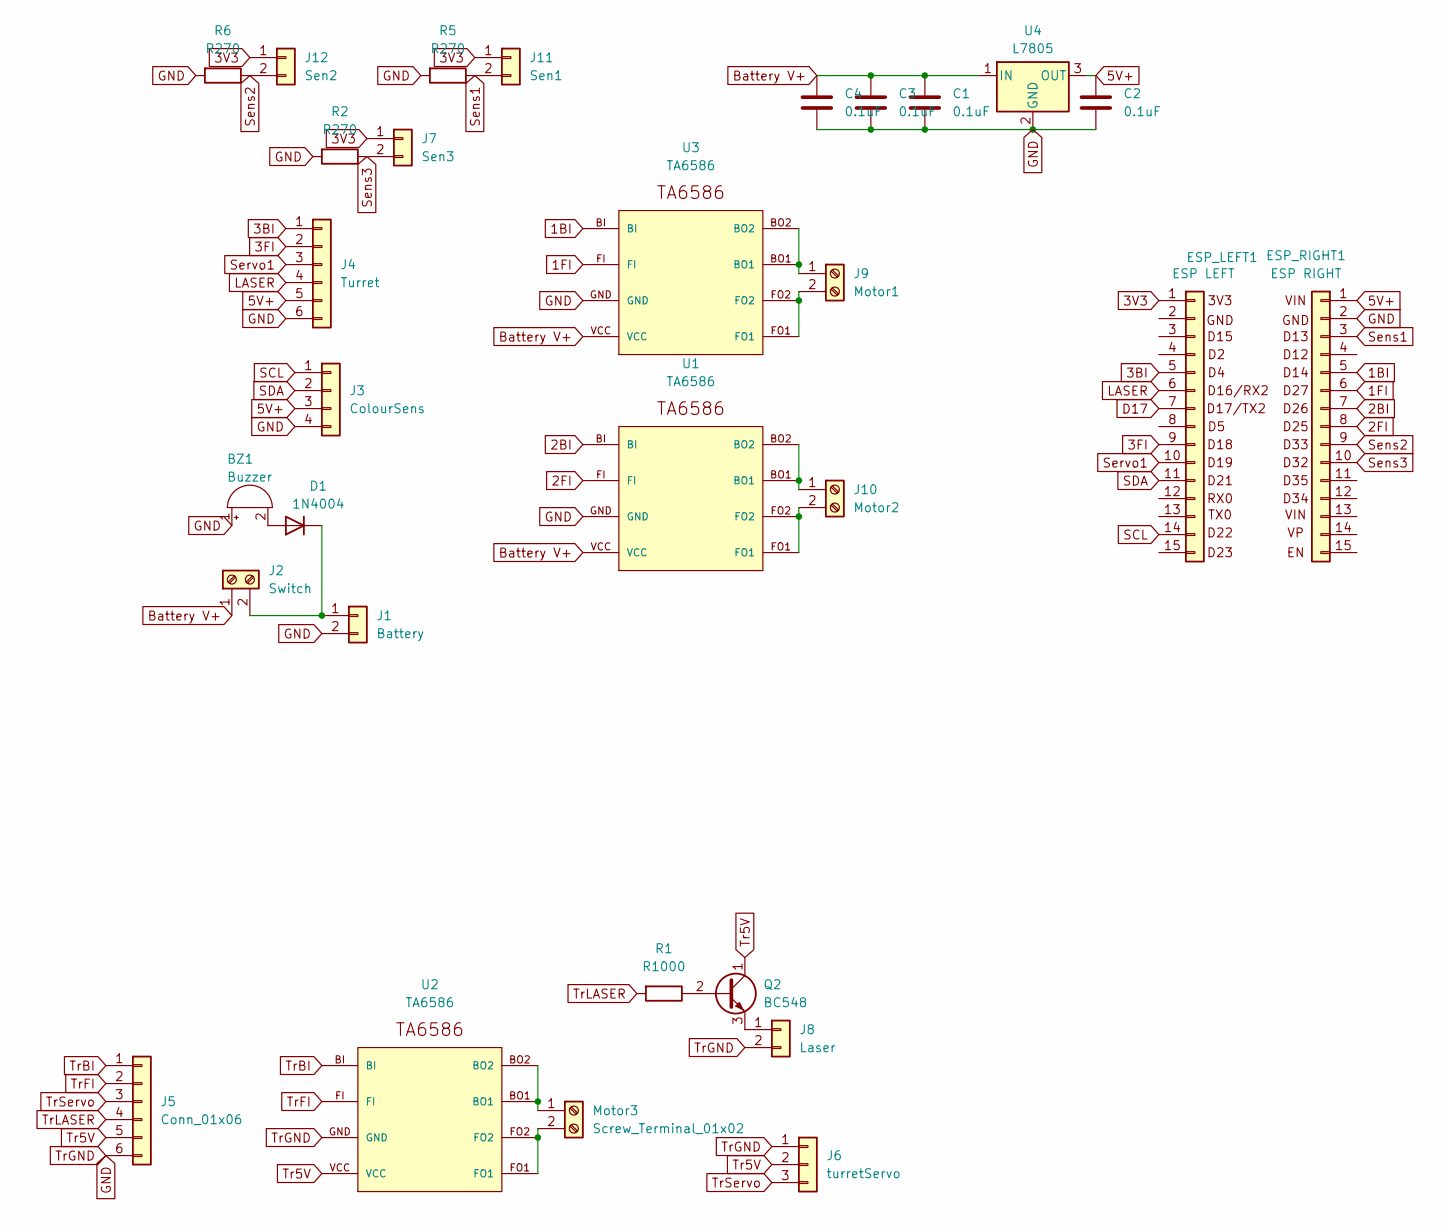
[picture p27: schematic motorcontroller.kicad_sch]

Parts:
BZ1: Buzzer; Buzzer_12x9.5RM7.6
C1, C2, C3, C4: 0.1uF; C_Rect_L9.0mm_W2.5mm_P7.50mm_MKT
D1: 1N4004; D_DO-41_SOD81_P10.16mm_Horizontal
ESP_LEFT1: ESP LEFT; PinHeader_1x15_P2.54mm_Vertical
ESP_RIGHT1: ESP RIGHT; PinHeader_1x15_P2.54mm_Vertical
J1: Battery; PinHeader_1x02_P2.54mm_Horizontal
J2: Switch; TerminalBlock_4Ucon_1x02_P3.50mm_Horizontal
J3: ColourSens; JST_XH_S4B-XH-A_1x04_P2.50mm_Horizontal
J4: Turret; JST_XH_S6B-XH-A_1x06_P2.50mm_Horizontal
J5: Conn_01x06; JST_XH_S6B-XH-A-1_1x06_P2.50mm_Horizontal
J6: turretServo; PinHeader_1x03_P2.54mm_Vertical
J7: Sen3; JST_XH_S2B-XH-A_1x02_P2.50mm_Horizontal
J8: Laser; PinHeader_1x02_P2.54mm_Vertical
J9: Motor1; TerminalBlock_4Ucon_1x02_P3.50mm_Horizontal
J10: Motor2; TerminalBlock_4Ucon_1x02_P3.50mm_Horizontal
J11: Sen1; JST_XH_S2B-XH-A_1x02_P2.50mm_Horizontal
J12: Sen2; JST_XH_S2B-XH-A_1x02_P2.50mm_Horizontal
Motor3: Screw_Terminal_01x02; TerminalBlock_4Ucon_1x02_P3.50mm_Horizontal
Q2: BC548; TO-92_Inline
R1: R1000; R_Axial_DIN0207_L6.3mm_D2.5mm_P7.62mm_Horizontal
R2, R5, R6: R270; R_Axial_DIN0207_L6.3mm_D2.5mm_P10.16mm_Horizontal
U1, U2, U3: TA6586; TA6586-FOOTPRINT
U4: L7805; TO-220F-3_Vertical

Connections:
1BI: ESP_RIGHT1.5 (D14), U3.BI
1FI: ESP_RIGHT1.6 (D27), U3.FI
2BI: ESP_RIGHT1.7 (D26), U1.BI
2FI: ESP_RIGHT1.8 (D25), U1.FI
3BI: ESP_LEFT1.5 (D4), J4.1
3FI: ESP_LEFT1.9 (D18), J4.2
3V3: ESP_LEFT1.1 (3V3), J7.1, J11.1, J12.1
5V+: C2.1, ESP_RIGHT1.1 (VIN), J3.3, J4.5, U4.3 (OUT)
Battery V+: C1.1, C3.1, C4.1, J2.1, U1.VCC, U3.VCC, U4.1 (IN)
D17: ESP_LEFT1.7 (D17)
GND: BZ1.1 (+), C1.2, C2.2, C3.2, C4.2, ESP_RIGHT1.2 (GND), J1.2, J3.4, J4.6, J5.6, J6.1, J8.2, R2.2, R5.2, R6.2, U1.GND, U2.GND, U3.GND, U4.2 (GND)
LASER: ESP_LEFT1.6 (D16), J4.4
unnamed: BZ1.2 (-), D1.2 (A)
unnamed: D1.1 (K), J1.1, J2.2
unnamed: J8.1, Q2.3 (E)
unnamed: J9.1, U3.BO1, U3.BO2
unnamed: J9.2, U3.FO1, U3.FO2
unnamed: J10.1, U1.BO1, U1.BO2
unnamed: J10.2, U1.FO1, U1.FO2
unnamed: Motor3.1, U2.BO1, U2.BO2
unnamed: Motor3.2, U2.FO1, U2.FO2
unnamed: Q2.2 (B), R1.1
SCL: ESP_LEFT1.14 (D22), J3.1
SDA: ESP_LEFT1.11 (D21), J3.2
Sens1: ESP_RIGHT1.3 (D13), J11.2, R5.1
Sens2: ESP_RIGHT1.9 (D33), J12.2, R6.1
Sens3: ESP_RIGHT1.10 (D32), J7.2, R2.1
Servo1: ESP_LEFT1.10 (D19), J4.3
Tr5V: J5.5, J6.2, Q2.1 (C), U2.VCC
TrBI: J5.1, U2.BI
TrFI: J5.2, U2.FI
TrLASER: J5.4, R1.2
TrServo: J5.3, J6.3

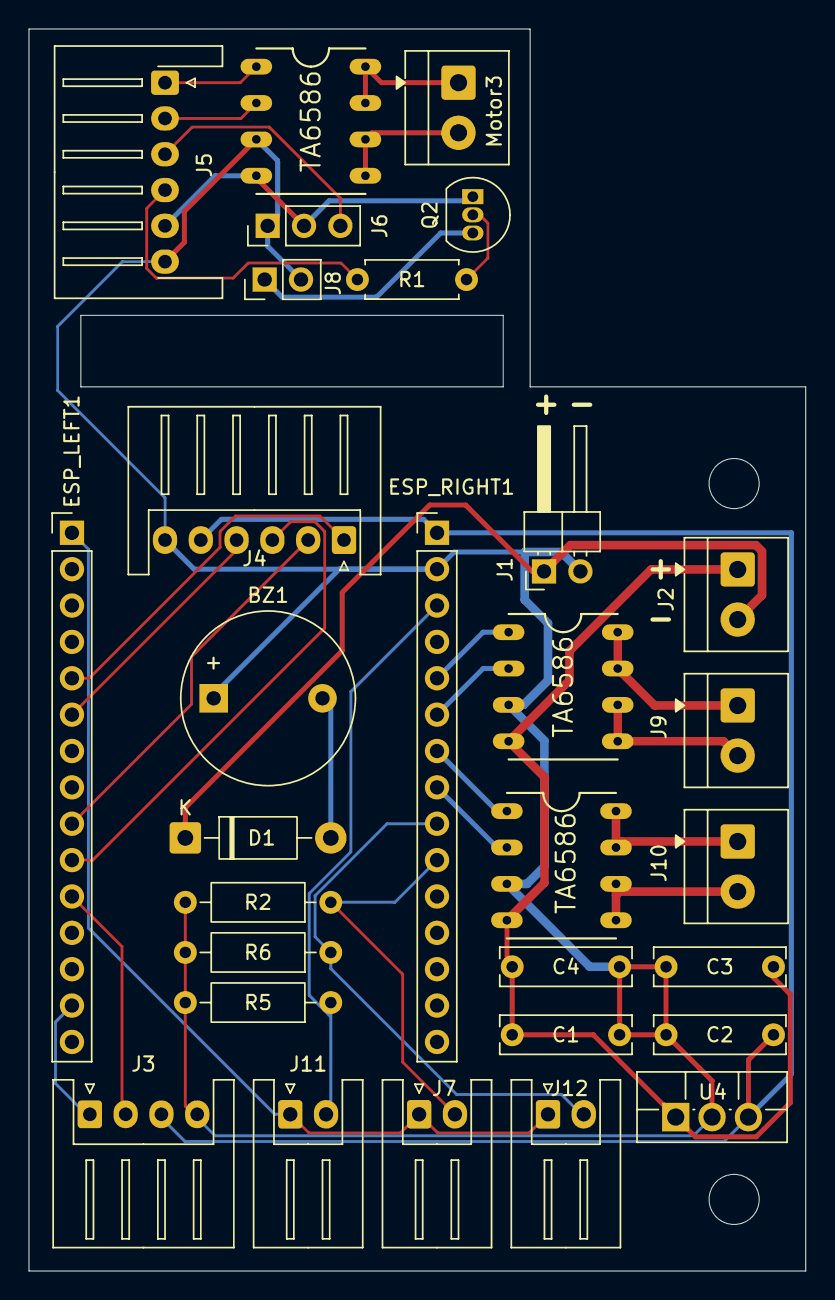
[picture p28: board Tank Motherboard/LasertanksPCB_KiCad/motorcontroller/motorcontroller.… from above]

Board: 2 copper layers, 54.2 x 86.8 mm, 30 parts (0 on the bottom side), 32 nets.

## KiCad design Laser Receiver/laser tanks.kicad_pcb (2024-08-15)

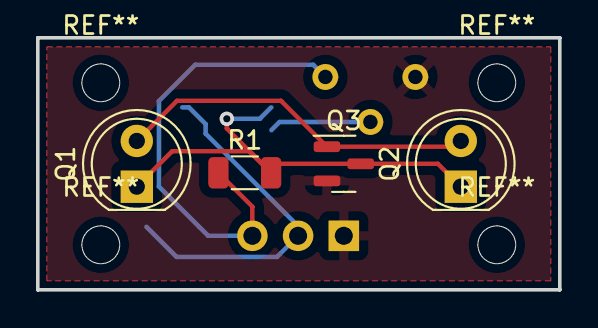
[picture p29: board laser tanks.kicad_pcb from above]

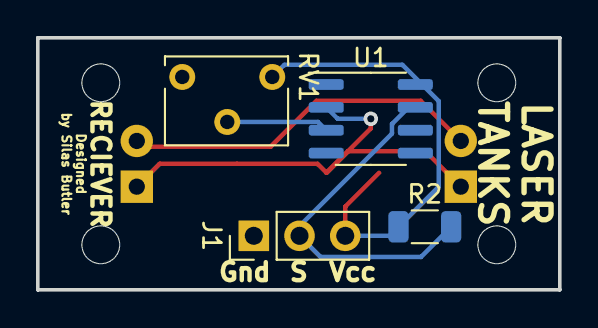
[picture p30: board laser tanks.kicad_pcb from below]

Board: 2 copper layers, 29.0 x 14.0 mm, 8 parts (4 on the bottom side), 6 nets.

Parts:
J1: Conn_01x03_Male; PinHeader_1x03_P2.54mm_Vertical
Q1, Q2: Q_Photo_NPN; LED_D5.0mm
Q3: BC846; SOT-23
R1, R2: 1k; R_1206_3216Metric
RV1: R_Potentiometer_Trim_US; Potentiometer_Vishay_T73XX_Horizontal
U1: LM311; SOIC-8_3.9x4.9mm_P1.27mm

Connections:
GND: J1.1, Q3.2 (E), RV1.3, U1.1 (GND), U1.4 (V-)
unnamed: J1.2, R2.2, U1.7
unnamed: Q1.1 (C), Q2.1 (C), Q3.3 (C), R1.2, U1.2 (+)
unnamed: Q1.2 (E), Q2.2 (E), Q3.1 (B)
unnamed: RV1.2, U1.3 (-)
VCC: J1.3, R1.1, R2.1, RV1.1, U1.8 (V+)

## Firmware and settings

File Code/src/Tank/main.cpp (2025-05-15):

#include <Arduino.h>
#include <ESP8266WiFi.h>
#include <espnow.h>
#include <pwm.h>

uint8_t controller_address[] = {0xFF, 0xFF, 0xFF, 0xFF, 0xFF, 0xFF};

#define MOTOR_A_POS 12
#define MOTOR_A_NEG 0

#define MOTOR_B_POS 4
#define MOTOR_B_NEG 14

// When an espnow message is recieved, the timeout is set to 15
// When > 0, the espnow_led is on
// When = 0, the espnow_led is off
// Decrements every loop
uint8_t espnow_led_timeout = 0;
#define ESPNOW_LED_TIMEOUT_TIME 30

// speed: [-127, 127] (Fastest going backwards, Fastest going forwards)
void SetLeftMotorSpeed(int8_t speed) {
	
	// Ranges between [0, 255]
	uint8_t absolute_speed = abs(speed) << 1;
	
	if (speed == 0) {
		digitalWrite(MOTOR_A_POS, HIGH);
		digitalWrite(MOTOR_A_NEG, HIGH);
	}
	
	if (speed < 0) {
		digitalWrite(MOTOR_A_NEG, HIGH);
		digitalWrite(MOTOR_A_POS, LOW);
		//analogWrite(MOTOR_A_POS, 255 - absolute_speed);
		return;
	}
	if (speed > 0) {
		digitalWrite(MOTOR_A_POS, HIGH);
		digitalWrite(MOTOR_A_NEG, LOW);
		//analogWrite(MOTOR_A_NEG, 255 - absolute_speed);
		return;
	}
	
	
	
}
void SetRightMotorSpeed(int8_t speed) {
	
	// Ranges between [0, 255]
	uint8_t absolute_speed = abs(speed) << 1;
	
	if (speed == 0) {
		digitalWrite(MOTOR_B_POS, HIGH);
		digitalWrite(MOTOR_B_NEG, HIGH);
	}
	
	if (speed < 0) {
		digitalWrite(MOTOR_B_NEG, HIGH);
		digitalWrite(MOTOR_B_POS, LOW);
		//analogWrite(MOTOR_B_POS, 255 - absolute_speed);
		return;
	}
	if (speed > 0) {
		digitalWrite(MOTOR_B_POS, HIGH);
		digitalWrite(MOTOR_B_NEG, LOW);
		//analogWrite(MOTOR_B_NEG, 255 - absolute_speed);
		return;
	}
	

}

void HandleMessage(uint8_t* message, uint8_t length) {
	
	if (length == 0) { return; }
	
	// Ping command
	if (message[0] == 0x00) {
		if (length != 2) { return; }
		
		if (message[1] == 0x00) {
			Serial.println("Ping recieved");
			uint8_t message[] = {0x00, 0x01};
			//SendMessage(message, 2);
		}
		
	}

	// Left motor speed
	if (message[0] == 0x01) {
		if (length != 2) { return; }
		
		int8_t motorSpeed = (message[1] % 0x40) << 1;
		uint8_t direction = (message[1] >> 6) & 0b1;
		if (direction == 1) {
			motorSpeed *= -1;
		}
		
		Serial.print("Motor_L: ");
		if (direction == 1) { Serial.print("-"); }
		else { Serial.print("+"); }
		Serial.println(motorSpeed);
		
		SetLeftMotorSpeed(motorSpeed);

	}
	
	// Right motor speed
	if (message[0] == 0x02) {
		if (length != 2) { return; }
		
		int8_t motorSpeed = (message[1] % 0x40) << 1;
		uint8_t direction = (message[1] >> 6) & 0b1;
		if (direction == 1) {
			motorSpeed *= -1;
		}
		
		Serial.print("Motor_R: ");
		if (direction == 1) { Serial.print("-"); }
		else { Serial.print("+"); }
		Serial.println(motorSpeed);
		
		SetRightMotorSpeed(motorSpeed);

	}
	
	
	
}

uint8_t serialMessage[255];
uint8_t serialMessageLength = 0;
// Reads the serial messages. If a complete message has been recieved it is passed on to HandleMessage.
void ProcessSerialMessages() {
	
	while (Serial.available() > 0) {
		uint8_t currentByte = Serial.read();
		
		// Start byte
		if (currentByte == 0xFF) {
			serialMessageLength = 0;
			continue;
		}
		
		// End byte
		if (currentByte == 0xFE) {
			HandleMessage(serialMessage, serialMessageLength);
			continue;
		}
		
		serialMessage[serialMessageLength] = currentByte;
		serialMessageLength ++;
		
		
	}

}

#define ESPNOW_MESSAGE_QUEUE_LENGTH 8
uint8_t* espnowMessage[ESPNOW_MESSAGE_QUEUE_LENGTH];
uint8_t espnowMessageLength[ESPNOW_MESSAGE_QUEUE_LENGTH];
void ESPNowCallback(uint8_t *mac_addr, uint8_t *data, uint8_t length) {
	
	espnow_led_timeout = ESPNOW_LED_TIMEOUT_TIME;
	
	uint8_t* espnowData = (uint8_t*)malloc(sizeof(uint8_t) * length);
	memcpy(espnowData, data, length);
	
	for (int i = 0; i < ESPNOW_MESSAGE_QUEUE_LENGTH; i ++) {
		if (espnowMessageLength[i] == 0) {
			espnowMessage[i] = espnowData;
			espnowMessageLength[i] = length;
			break;
		}
	}
	
}
void InitESPNow() {
	
	WiFi.disconnect();
	WiFi.mode(WIFI_STA);
	esp_now_init();
	
	// ESPNow has initialised successfully here
	esp_now_set_self_role(ESP_NOW_ROLE_SLAVE);
	esp_now_register_recv_cb(ESPNowCallback);
	
	
}

uint8_t pulseCounter = 0;
void Buzz(int duration, int semitone) {
	
	int freq = 440 * pow(1.05946, semitone);
	
	analogWriteFreq(freq);
	SetRightMotorSpeed(20);
	SetLeftMotorSpeed(-20);
	delay(duration);
	SetRightMotorSpeed(0);
	SetLeftMotorSpeed(0);
	//delay(duration >> 1);
}



void setup() {
	
	Serial.begin(9600);
	Serial.println();
	Serial.println();
	Serial.println("This is the Tank board");
	Serial.print("MAC Address: ");
	Serial.println(WiFi.macAddress());
	
	InitESPNow();

	pinMode(LED_BUILTIN, OUTPUT);
	pinMode(LED_BUILTIN_AUX, OUTPUT);
	
	pinMode(MOTOR_A_POS, OUTPUT);
	pinMode(MOTOR_A_NEG, OUTPUT);
	
	pinMode(MOTOR_B_POS, OUTPUT);
	pinMode(MOTOR_B_NEG, OUTPUT);
	
	
	int duration = 30;
	int tune[] = {-5, 0, 4, 7, 12, -50, -5, 0, 4, 7, 12, -50, -5, 0, 4, 7, 12};
	int length = 17;

	
	//int duration = 120;
	//int tune[] = {2, 2, 14, -50, 9, -50, -50, 8, -50, 7, -50, 5, -50, 2, 5, 7};
	//int length = 16;
	
	
	for (int i = 0; i < length; i ++) {
		if (tune[i] == -50) {
			delay(duration);
			continue;
		}
		Buzz(duration, tune[i]);
	}
	
	
	analogWriteFreq(25000);
	
	SetLeftMotorSpeed(0);
	SetRightMotorSpeed(0);
	
	
}
void loop() {
	
	digitalWrite(MOTOR_A_POS, HIGH);
	digitalWrite(MOTOR_A_NEG, HIGH);
	digitalWrite(MOTOR_B_POS, HIGH);
	digitalWrite(MOTOR_B_NEG, HIGH);
	
	// Turn the builtin led on and off
	if (espnow_led_timeout > 0) {
		digitalWrite(LED_BUILTIN, HIGH);
		espnow_led_timeout -= 1;
	}
	else {
		digitalWrite(LED_BUILTIN, LOW);
	}
	
	// LED Heartbeat
	if (pulseCounter == 0 || pulseCounter == 40) {
		digitalWrite(LED_BUILTIN_AUX, LOW);
		delay(5);
		digitalWrite(LED_BUILTIN_AUX, HIGH);
		delay(5);
	}
	pulseCounter ++;
	pulseCounter %= 160;
	
	// Read and recieve serial messages
	ProcessSerialMessages();
	
	// Check if ESPNow messages are ready to be handled
	for (int i = 0; i < ESPNOW_MESSAGE_QUEUE_LENGTH; i ++) {
		if (espnowMessageLength[i] > 0) {
			HandleMessage(espnowMessage[i], espnowMessageLength[i]);
			free(espnowMessage[i]);
			espnowMessageLength[i] = 0;
		}
	}
	
	delay(5);
	
}

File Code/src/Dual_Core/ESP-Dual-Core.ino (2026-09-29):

// Select Esp32 Dev Module - esp32_bluepad32 for the board when uploading
#include <Bluepad32.h>
#include <Arduino.h>
#include <ESP32Servo.h>

void coreTaskZero(void * pvParameters);
void coreTaskOne(void * pvParameters);

uint8_t LASER1 = 16;
uint8_t LASER2 = 17;
uint8_t PHOTO = 15; //Phototransistor
uint8_t BARREL = 19;
uint8_t THRESHPIN = 35;
uint8_t JS_DEADZONE = 50; // Joystick deadzone
uint8_t RJS_DEADZONE = 50; // Right Joystick deadzone (turret joystick)
uint16_t LASER_THRESH = 200;

// thresh could be 560
int detectionThresh = 300;

ControllerPtr myController = nullptr;
Servo barrelServo;

// TA6586 Control pins
// The Motor driver is a Half H-Brdige, with to input pins
// Having one high and the other lower will cause the motor to spin one way
// Switch polarity to change directions
// When both are high the motor will brake **
// When both are Low the motor will coast ** 
const int BI_L = 14;
const int FI_L = 27;
const int BI_R = 26;
const int FI_R = 25;

// Turret Left and Right pins
const int TI_L = 4;
const int TI_R = 18;

//Intitalising values
int leftPWM = 0;
int rightPWM = 0;
int throttle = 0;
int turn = 0;

void onConnectedController(ControllerPtr ctl) {
  if (myController == nullptr) {
    Serial.print("CALLBACK: Controller is connected, index=");
    Serial.println(ctl->index());
    // Make sure motors stop when connected
    digitalWrite(FI_L, 0);
    digitalWrite(FI_R, 0);
    digitalWrite(BI_L, 0);
    digitalWrite(BI_R, 0);
    myController = ctl;
  }
}

void onDisconnectedController(ControllerPtr ctl) {
  if (myController == ctl) {
    Serial.print("CALLBACK: Controller is disconnected from index=");
    Serial.println(ctl->index());
    // Stop motors when controller disconnects
    digitalWrite(FI_L, 0);
    digitalWrite(FI_R, 0);
    digitalWrite(BI_L, 0);
    digitalWrite(BI_R, 0);
    myController = nullptr;
  }
}

void setup()
{
  Serial.begin(115200);

  BP32.setup(&onConnectedController, &onDisconnectedController);
  BP32.forgetBluetoothKeys();

  // Initialise Servo
  barrelServo.attach(BARREL);

  //Intitalising Pins
  pinMode(FI_L, OUTPUT);
  pinMode(FI_R, OUTPUT);
  pinMode(BI_L, OUTPUT);
  pinMode(BI_R, OUTPUT);

  // put your setup code here, to run once:
  xTaskCreatePinnedToCore(
    coreTaskZero,
    "Main Loop",
    10000,
    NULL,
    2,
    NULL,
    0
  );

  xTaskCreatePinnedToCore(
    coreTaskOne,
    "Laser",
    10000,
    NULL,
    2,
    NULL,
    1
  );
}

inline bool controllerAvailable()
{
  if (myController && myController->isConnected())
  {
    return true;
  }

  return false;
}

inline uint8_t isInDeadzone(int pwmVal)
{
  return abs(pwmVal) <= JS_DEADZONE;
}

void moveMotor(int motorPWM, uint8_t frontPin, uint8_t backPin)
{
  // If in deadzone, set both pins to low
  if (isInDeadzone(motorPWM))
  {
    analogWrite(frontPin, 0);
    analogWrite(backPin, 0);
    return;
  }

  // For PWM >= 0, move forward, otherwise move backwards
  if (motorPWM >= 0)
  {
    analogWrite(frontPin, motorPWM);
    analogWrite(backPin, 0); // using digitalWrite(Pin, LOW) here causes problems for some reason so keep it as an analogWrite(Pin, 0)
  }
  else
  {
    analogWrite(backPin, -motorPWM); // makes PWM value positive
    analogWrite(frontPin, 0);
  }
}

void shootLaser(uint8_t laser_pin, uint8_t value)
{
  // Throttle 0-1023
  if (!controllerAvailable())
  {
    return;
  }
  
  uint16_t throttle = myController->throttle();

  // printf("Throttle value is: %d\n", throttle);

  if (throttle > LASER_THRESH)
  {
    analogWrite(laser_pin, value);
  }
  else
  {
    // HIGH turns the laser off for PNP transistor
    analogWrite(laser_pin, 255);
    //digitalWrite(laser_pin, HIGH);
  }
}

void driveLoop()
{
  // Check if the controller exists and is connected
  // No longer uses myControllerhasUpdate as updates were not being sent often enough and readings were off
  if (!controllerAvailable())
  {
    moveMotor(0, FI_R, BI_R);
    moveMotor(0, FI_L, BI_L);
    return;
  }

  // Converts the axis signed 9 bit (512) reading into a signed 8 bit(256) reading
  turn = myController->axisX() >> 1;
  throttle = -myController->axisY() >> 1; // Top is negtive for Y-axis, so it need to be inverted
  
  // Converting controller readings to PWM values for the tank steer using two motors
  // Serial.println(turn);
  // Serial.println(throttle);
  leftPWM = throttle + turn;
  rightPWM = throttle - turn;
  leftPWM = constrain(leftPWM, -255, 255);
  rightPWM = constrain(rightPWM, -255, 255);

  moveMotor(rightPWM, FI_R, BI_R);
  moveMotor(leftPWM, FI_L, BI_L);
}

void moveBarrelServo()
{
  if (!controllerAvailable())
  {
    return;
  }

  int16_t rawAxisY = myController->axisRY();
  uint8_t min = 0, max = 70;
  uint8_t zeroPos = (max - min) / 2;

  // Up is -512 & Down is 511
  printf("Up down is: %d\n", rawAxisY);

  // If in the deadzone, return to zero / home position
  if (abs(rawAxisY) < RJS_DEADZONE / 2)
  {
    // printf("Moving servo to zero pos\n");

    barrelServo.write(zeroPos);
  }
  else
  {
    // Max and min turret angles
    uint8_t servoPos = (rawAxisY + 512) * (max - min) / 1023;

    servoPos = constrain(servoPos, min, max);

    // printf("Moving servo to pos: %d\n", servoPos);
    barrelServo.write(servoPos);
  }
}

void moveTurretServo()
{
  if (!controllerAvailable())
  {
    return;
  }

  // Gets the raw X axis values
  int16_t rawAxisX = myController->axisRX();

  int16_t max = 128, min = -128;
  
  
  int16_t turnPWM = (rawAxisX + 512) * (max - min) / 1023 + min;

  // Constrain max and min to ensure PWM does not go over them
  turnPWM = constrain(turnPWM, min, max);

  moveMotor(turnPWM, TI_L, TI_R);
}

void loop()
{
  // put your main code here, to run repeatedly:
  // int resVal = analogRead(4);
  // printf("Potentiometer Val: %d\n", resVal);
}

void coreTaskZero(void * pvParameters)
{
  pinMode(LASER1, OUTPUT);
  pinMode(LASER2, OUTPUT);

  while(1)
  {
    BP32.update();

    // Write PWM signals to Laser pins
    shootLaser(LASER1, 100);
    // analogWrite(LASER1,0);
    // digitalWrite(LASER1, 255);
    // analogWrite(LASER1,100);
    analogWrite(LASER2,200);
    
    driveLoop();
    moveBarrelServo();
    moveTurretServo();

    // detectionThresh = analogRead(THRESHPIN);
    
    vTaskDelay(pdMS_TO_TICKS(1));
  }
}
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

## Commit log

2024-03-16 Initial commit
    Added tank project project environment.
    This is just an interrupt test which doesnt work :(
    When programming the controller and server, probably going to use the same repository and just have it in different source files.
2024-03-22 Started main program structure
    Started main structure
    Added reading from serial, debugging over serial, and switch wrappers around serial
    Started Laser system, added in shoot functionality
    Started Comms system, added in 'F' to fire the laser
    Cleaned up structure
2024-04-12 Cleanup PWM and Interrupt
    Took the PWM logic out of Drive.c and moved it to PWM.c for more abstraction
    Added the shopping list
    [Laser Tanks Shopping List.xlsx]
2024-08-01 Update Links.txt
    CAD
2024-08-01 Updated motor speeds and mapping
2024-08-10 Added Tank V1 model
    [Laser Tank V1.stl]
2024-08-15 Create 3D Printing files
2024-08-15 Organising 3d files
    [Laser Tank V1.stl, Motor.step]
2024-08-15 Uploaded receiver circuits
    [laser tanks-B_Cu.gbr, laser tanks-B_Mask.gbr, laser tanks-B_Paste.gbr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]
2024-08-17 Re organised GIT structure
    [Laser Tank V1.stl, Laser Tanks Shopping List.xlsx, Motor.step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]
2024-08-23 Updated: Frame
2024-08-23 Network Frame Updated
2024-08-29 Test ESP now on ESP32
2024-09-21 Added Tank Model V2
    [Back track holder.stl, Back track.stl, Front track holder.stl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]
2024-09-26 Added motor driver circuit documentation
2024-10-04 Added battery readout to ControllerPC
2025-01-21 Fixed controller code
    The controller now works as expected. The only issue was assigning the analog pins as input pins. That mucks with something, im not sure what
    [main.cpp]
2025-01-23 2 New CAD Versions!!
    Wake up babe, new Laser Tanks commit dropped.
    Added Obsidian documentation
    Added V3 and V4 models
    [Back track holder.stl, Back track.stl, Front track holder L.stl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]
2025-02-10 Added Tank Model V4
    [Back track holder.stl, Front track holder L.stl, Front track holder R.stl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]
2025-02-10 Added Tank Motherboard V2
    Redesigned the motherboard of the last tank to include a spot for the ESP8266 to go. Also improved all aspects of the circuit!
2025-02-13 Improved Tank Motherboard V2
    Added reverse voltage protection in case you connect the LiPo backwards.
    Added a switch to connect / disconnect LiPo +
2025-03-06 Controller
    Fixed Controller again
    [main.cpp]
2025-03-19 Almost finished Tank Motherboard V3
    Almost finished routing the new PCB
    Just gotta add the finishing touches
2025-08-07 Create Laser Tanks Tank Motherboard.pdf
2025-08-07 Added MotherboardV3 pdf schematic
2025-08-14 Added Altered PCB V4
2025-08-14 Added MotherBoard V4 Gerber
2026-05-14 Added Dual-Core code for detecting laser PWM on isolated core
2026-06-21 Renamed How to write and upload code.md to README.md
    Renamed the aforementioned markdown to readme to allow for easy merging between upstream and current fork.
